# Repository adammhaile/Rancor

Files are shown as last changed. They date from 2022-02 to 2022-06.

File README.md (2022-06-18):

# Rancor 3D Printer

Rancor is a project that came about from being inspired by seeing all the awesome projects at MRRF 2021 and is my first ground-up 3D printer design. It is an IDEX machine with a "spared no expense" and "there's no such thing as too much feature creep" design philosophy. Learning to CNC machine aluminium with my new [MilkCr8 CNC](https://github.com/Makers-On-Tap/milkcr8-cnc) was also a major factor, so if a component *could* be machined out of 1/4" aluminum tooling plate, it was. It was never designed to be manufactured and mainly exists as somethingt to show off.

## Specs

- Cartesian IDEX motion system
- 45 parts custom machined from aluminum tooling plate
- Cold-swappable tools require only 3 bolts and a 14-pin Molex Mini-Fit connector
- 5 currently configured tools that can be used
    - 2x E3D Hemera & Revo
    - 3x E3D Hemera & copper block, Slice 50W heater, Bondtech CHT nozzle (1.0mm, 1.4mm, 1.8mm)
- 330x320x600 mm print volume
- Prusa SuperPINDA ABL probe
- 0.9° LDO 42STH60-2004MAC Motors for each axis
- LDO MGN12 Linear Rails
- PTFE coated LDO leadscrews for Z
- Mandala Rose Works 6.35mm MIC6 cast aluminum bed (Railcore)
- Mandala Rose Works Z axis bed yokes (Railcore)
- Mandala Rose Works Z Oldham Wobblers (Railcore)
- 750W 120V AC Keenovo Bed Heater
- Duet 6HC mainboard with Duet 3HC expansion to drive all 9 motors
- 930x550x960 mm outter dimensions (excluding tool cables)
- 7.9" 400x1280 LCD display for g-code scrolling
- 13.3" 1080x1920 LCD touch display to show the Duet DWC interface
- 2x Raspberry Pi 4 - One for Duet SBC and one running Android for DWC display
- Filament sensors for each tool, based on the Prusa Mini sensor
- Internal network between the two Pi 4's using a Linksys router that provides on-site WiFi
- Ethernet connection for Duet SBC Pi for normal network connectivity
- Teensy 3.2 managed "voice" output controlled via a Duet UART connection

## CAD

All of the CAD for this project was done in Fusion 360 and the files (both F360 and STEP) can be found on [this release page](https://github.com/adammhaile/Rancor/releases/tag/cad_release).

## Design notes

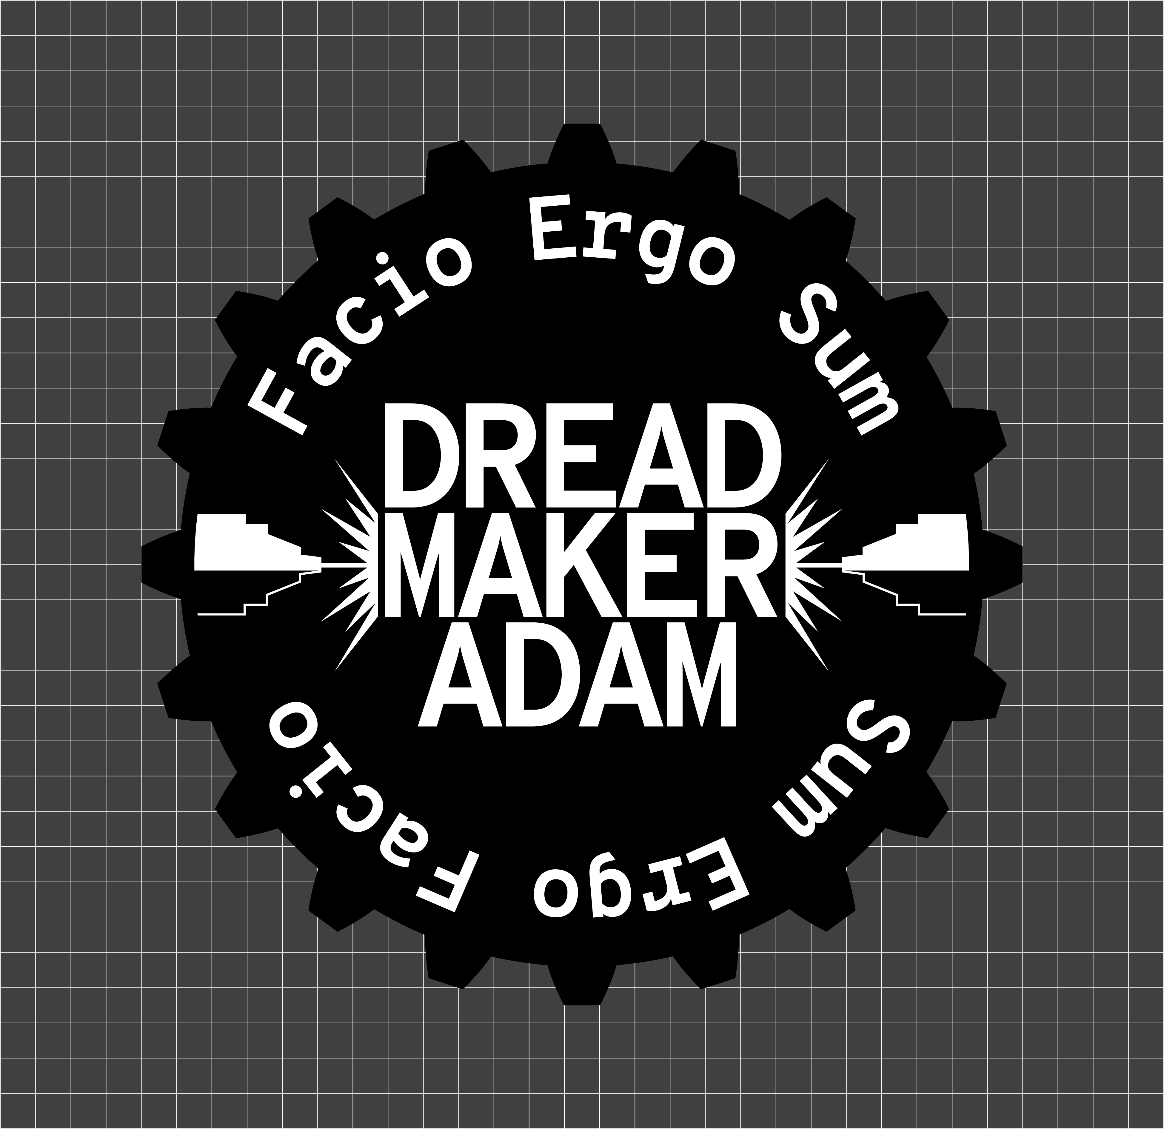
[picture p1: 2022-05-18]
PrusaSlicer/BedTexture.png

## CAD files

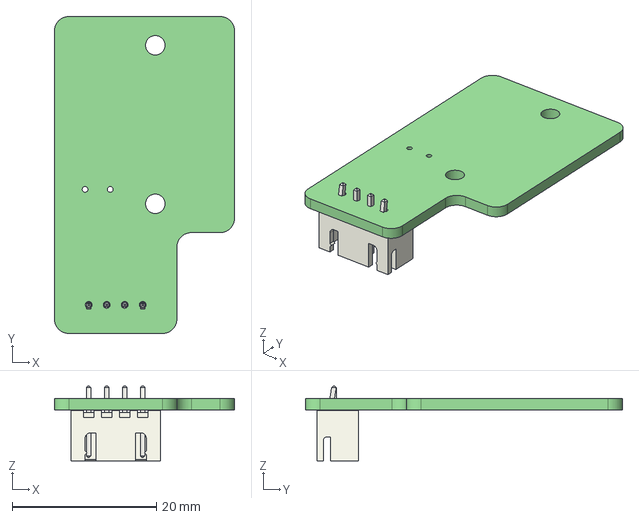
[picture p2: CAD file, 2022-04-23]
larson_vu/larson_vu_pcb/larson_vu_pcb.step
25.0 x 44.0 x 10.4 mm
larson_vu_pcb PCB

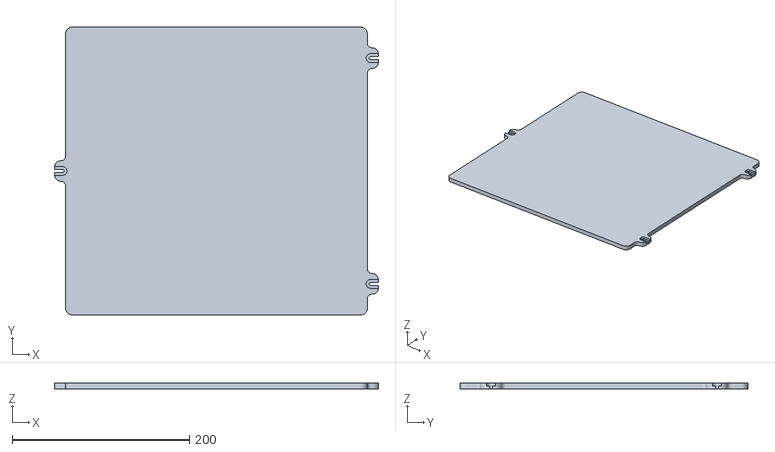
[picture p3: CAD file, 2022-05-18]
PrusaSlicer/BedModel.stl
366.0 x 325.0 x 6.35

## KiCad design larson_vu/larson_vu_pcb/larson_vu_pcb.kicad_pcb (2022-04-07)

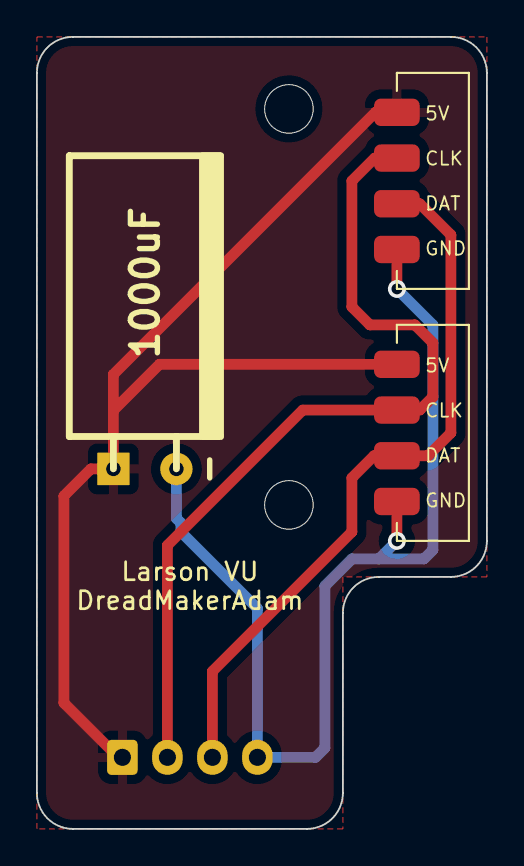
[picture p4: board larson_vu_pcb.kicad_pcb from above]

Board: 2 copper layers, 25.0 x 44.0 mm, 6 parts (1 on the bottom side), 4 nets.

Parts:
C1: 1000uF; CP_8x15mm_horiz-L
H1, H2: MountingHole; MountingHole_2.7mm_M2.5
J1: FromController; JST_XH_B4B-XH-A_1x04_P2.50mm_Vertical
J2, J3: ToStrip; APA102_STRIP

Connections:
5V: C1.1, J1.1, J2.1, J3.1
CLK: J1.2, J2.2, J3.2
DATA: J1.3, J2.3, J3.3
GND: C1.2, J1.4, J2.4, J3.4

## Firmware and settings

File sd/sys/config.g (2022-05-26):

; Load global vars
M98 P"globals.g"

; General preferences
G90                                                         ; send absolute coordinates...
M83                                                         ; ...but relative extruder moves
M550 P"Rancor"                                              ; set printer name

; Larson VU Serial Config
M575 P1 B57600 S2                                           ; Setup UART on IO_0 to 57600 baud

; Audio Player Serial Config
M575 P2 B57600 S2                                           ; Setup UART on IO_1 to 57600 baud

; Setup Lights
M950 P0 C"0.out9" Q4000

; Setup Servos
M950 S1 C"0.io7.out"
M280 P1 S100

; Wait a moment for the CAN expansion boards to start
G4 S2

; Drives
M569 P0.0 S0                                                ; Left Y
M569 P0.1 S1                                                ; Left X
M569 P0.2 S0                                                ; Left Extruder
M569 P0.3 S1                                                ; Left Z
M569 P0.4 S1                                                ; Right Rear Z
M569 P0.5 S1                                                ; Right Front Z
M569 P1.0 S1                                                ; Right Y
M569 P1.1 S1                                                ; Right X
M569 P1.2 S0                                                ; Right Extruder

M584 X0.1 U1.1 Y0.0:1.0 Z0.3:0.4:0.5 E0.2:1.2               ; set drive mapping
M350 X16 U16 Y16 Z16 E16:16 I1                              ; configure microstepping with interpolation
M92  X160 U160 Y160 Z1600 E397:397                          ; set steps per mm
M566 X400 U400 Y400 Z100 E1500:1500                         ; set maximum instantaneous speed changes (mm/min)
M203 X10800 U10800 Y10800 Z900 E3600:3600                   ; set maximum speeds (mm/min)
M201 X500 U500 Y500 Z100 E1500                             	; set accelerations (mm/s^2)
M906 X1400 U1400 Y1400 Z1200 E1100:1100 I75                 ; set motor currents (mA) and motor idle factor in per cent
;M84 S30                                                    ; Set idle timeout

;Leadscrew locations
M671 X-13.7:343.8:343.8 Y160:287.5:32.5 S7.5

; Axis Limits
; TODO - these are wild guesses at this point for X
; will need to change mins to negatives
M208 S1 X-85 U0 Y0 Z-2                                            ; set axis minima
M208 S0 X405 U450 Y345 Z{global.zsize}                            ; set axis maxima

; Endstops
M574 X1 S1 P"0.io2.in"                                        ; X homes low end
M574 U2 S1 P"1.io2.in"                                        ; U homes high end
M574 Y1 S1 P"0.io3.in+1.io3.in"                               ; Y has dual motors and endstops
; TODO - setup homing files https://duet3d.dozuki.com/Wiki/ConfiguringMultipleIndependentXcarriagesCartesian#Section_Homing_files

; Z-Probe
M558 P5 C"^0.io5.in" H2.5 F250 T6000                            ; set Z probe type to switch and the dive height + speeds
G31 P500 X0 Y0 Z1.2                                   ; set Z probe trigger value, offset and trigger height
M557 X15:315 Y20:300 S75:70                                    ; define mesh grid

; Heaters
; Bed
M308 S0 P"0.temp0" Y"thermistor" T100000 B4240                ; configure sensor 0 as thermistor on pin temp0
M950 H0 C"0.out0" T0                                          ; create bed heater output on out0 and map it to sensor 0
M307 H0 B0 R0.611 C647.0 D2.25 S1.00                          ; enable bang-bang mode for the bed heater and set PWM limit
M140 H0                                                     ; map heated bed to heater 0
M143 H0 S120                                                ; set temperature limit for heater 0 to 120C

; Left
M308 S1 P"0.temp1" Y"thermistor" T100000 B4725 C7.06e-8       ; configure sensor 1 as thermistor on pin temp1
M950 H1 C"0.out1" T1                                          ; create nozzle heater output on out1 and map it to sensor 1
; M307 H1 R2.616 K0.237:0.348 D5.69 E1.35 S1.00 B0 V23.9      ; disable bang-bang mode for heater  and set PWM limit
; M143 H1 S285                                                ; set temperature limit for heater 1 to 280C

; Right
M308 S2 P"1.temp0" Y"thermistor" T100000 B4725 C7.06e-8     ; configure sensor 2 as thermistor on pin 1.temp0
M950 H2 C"1.out0" T2                                        ; create nozzle heater output on 1.out0 and map it to sensor 2
; M307 H1 R2.616 K0.237:0.348 D5.69 E1.35 S1.00 B0 V23.9      ; disable bang-bang mode for heater  and set PWM limit
; M143 H2 S285                                                ; set temperature limit for heater 2 to 280C

; Fans
; left HEF
M950 F0 C"0.out7"                                             ; create fan 0 on pin out7 and set its frequency
M106 P0 S1 H1 T45                                         ; set fan 0 value. Thermostatic control is turned on
; Left PCF
M950 F1 C"0.out8"                                             ; create fan 1 on pin out8 and set its frequency
M106 P1 S0 H-1                                              ; set fan 1 value. Thermostatic control is turned off
; Right HEF
M950 F2 C"1.out7"                                           ; create fan 2 on pin 1.out7 and set its frequency
M106 P2 S1 H2 T45                                         ; set fan 2 value. Thermostatic control is turned on
; Right PCF
M950 F3 C"1.out8"                                           ; create fan 3 on pin 1.out8 and set its frequency
M106 P3 S0 H-1                                               ; set fan 3 value. Thermostatic control is turned on

; Tools
; Left
M563 P0 S"Left" D0 X0 H1 F1                                    ; define tool 0
; G10 P0 X-71.5 Y-20.6 Z0                                        ; set tool 0 axis offsets
G10 P0 X0 Y0 Z0
G10 P0 R0 S0                                                   ; set initial tool 0 active and standby temperatures to 0C

M591 D0 P1 C"0.io4.in" S0								; setup T0 filament sensor

; Right
M563 P1 S"Right" D1 X3 H2 F3                                   ; define tool 1
; G10 P1 U-0.3 Y-20.6 Z0.35                                      ; set tool 1 axis offsets
G10 P1 U0 Y0 Z0
G10 P1 R0 S0                                                   ; set initial tool 1 active and standby temperatures to 0C

M591 D1 P1 C"1.io5.in" S0								; setup T1 filament sensor

; extra sensors
M308 S10 Y"mcu-temp" A"MCU"                           ; defines sensor 10 as MCU temperature sensor

; set base tool names
M98 P"tools/t0.g" 
M98 P"tools/t1.g"
M98 P"tools/bed.g"

; load variable tool configs
M98 P"tools/setup.g"

; Ensure T0 loaded
M98 P"soft_load_tool.g" S0

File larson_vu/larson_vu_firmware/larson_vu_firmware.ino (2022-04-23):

#include <FastLED.h>

#include <EEPROM.h>
#include <Arduino.h>

template <class T>
int EEPROM_writeAnything(int ee, const T &value)
{
    const byte *p = (const byte *)(const void *)&value;
    unsigned int i;
    for (i = 0; i < sizeof(value); i++)
        EEPROM.write(ee++, *p++);
    return i;
}

template <class T>
int EEPROM_readAnything(int ee, T &value)
{
    byte *p = (byte *)(void *)&value;
    unsigned int i;
    for (i = 0; i < sizeof(value); i++)
        *p++ = EEPROM.read(ee++);
    return i;
}

#define ANIM_AUDIO 0
#define ANIM_LARSON_RED 1
#define ANIM_LARSON_ORANGE 2
#define ANIM_LARSON_YELLOW 3
#define ANIM_LARSON_GREEN 4
#define ANIM_LARSON_BLUE 5
#define ANIM_LARSON_PURPLE 6
#define ANIM_LARSON_RAINBOW 7

#define MODE_OFF 0
#define MODE_SOUND 1
#define MODE_LARSON 2
#define MODE_BOTH 3

#define CONFIGCHECK 14
struct config_t
{
    uint8_t mode; // 0=off, 1=sound only, 2=larson only, 3=both
    uint8_t cur_anim;
} config;

void writeConfig()
{
    EEPROM_writeAnything(1, config);
}

void readConfig()
{
    EEPROM_readAnything(1, config);
}

void writeDefaultConfig()
{
    config.mode = MODE_BOTH;
    config.cur_anim = ANIM_LARSON_RED;
}

#define STROBE 4
#define RESET 5
#define DC_One A0
#define DC_Two A1

// audio vars
int FreqL[7];
int FreqR[7];

int SumL = 0;
int SumR = 0;

bool mono_audio = true;

// audio clamp values
#define MIN_LEVEL 100
#define MAX_LEVEL 350
#define OUT_MIN 0
#define OUT_MAX 20

// LED stuff
#define NUM_LEDS 40
#define DATA_PIN SPI_DATA
#define CLOCK_PIN SPI_CLOCK
CRGB leds[NUM_LEDS];

uint8_t led_r_start = (NUM_LEDS / 2);
uint8_t led_l_start = led_r_start - 1;

uint8_t last_anim = 1;

unsigned long last_frame = 0;
#define FRAME_TIME 5

unsigned long last_audio = 0;
#define AUDIO_COOLDOWN 1000

int step = 0;

String serial_input;

/********************Setup Loop*************************/
void setup()
{
    // if (EEPROM.read(0) != CONFIGCHECK)
    // {
    //     EEPROM.write(0, CONFIGCHECK);
    //     writeDefaultConfig();
    // }
    readConfig();

    serial_input = "";

    FastLED.addLeds<SK9822, DATA_PIN, CLOCK_PIN, BGR>(leds, NUM_LEDS).setCorrection(TypicalLEDStrip);
    FastLED.setBrightness(192);

    // Set spectrum Shield pin configurations
    pinMode(STROBE, OUTPUT);
    pinMode(RESET, OUTPUT);
    pinMode(DC_One, INPUT);
    pinMode(DC_Two, INPUT);

    // Initialize Spectrum Analyzers
    digitalWrite(STROBE, LOW);
    digitalWrite(RESET, LOW);
    delay(5);

    Serial.begin(57600);
    // while (!Serial) { delay(1); }

    set_anim(config.cur_anim);
}

void FetchAudio()
{
    digitalWrite(RESET, HIGH);
    delayMicroseconds(200);
    digitalWrite(RESET, LOW);
    delayMicroseconds(200);

    static int freq_amp = 0;
    for (freq_amp = 0; freq_amp < 7; freq_amp++)
    {
        digitalWrite(STROBE, HIGH);
        delayMicroseconds(50);
        digitalWrite(STROBE, LOW);
        delayMicroseconds(50);

        FreqL[freq_amp] = analogRead(DC_One);
        FreqR[freq_amp] = analogRead(DC_Two);
    }

    static int i = 0;
    SumL = SumR = 0;
    for (i = 0; i < 7; i++)
    {
        SumL += FreqL[i];
        SumR += FreqR[i];
    }

    SumL /= 7;
    SumR /= 7;

    SumL = map(SumL, MIN_LEVEL, MAX_LEVEL, OUT_MIN, OUT_MAX);
    SumL = constrain(SumL, OUT_MIN, OUT_MAX);
    SumR = map(SumR, MIN_LEVEL, MAX_LEVEL, OUT_MIN, OUT_MAX);
    SumR = constrain(SumR, OUT_MIN, OUT_MAX);

    if (mono_audio)
    {
        SumR = SumL;
    }
}

void set(uint8_t i, CRGB color)
{
    if (i >= 0 && i < NUM_LEDS)
    {
        leds[i] = color;
    }
}

void anim_audio()
{
    static int x = 0;
    static int c = 0;

    FastLED.clear();

    c = 0;
    for (x = led_l_start; x >= 0; x--)
    {
        if (SumL > c)
        {
            leds[x] = CRGB::Orange;
        }
        else
        {
            break;
        }
        c++;
    }

    c = 0;
    for (x = led_r_start; x < NUM_LEDS; x++)
    {
        if (SumR > c)
        {
            leds[x] = CRGB::Orange;
        }
        else
        {
            break;
        }
        c++;
    }

    FastLED.show();
}

uint8_t larson_tail = 15;
int8_t larson_dir = -1;
uint8_t larson_fade = 256 / (larson_tail + 2);
uint8_t larson_divider = 6;
uint8_t larson_sub_step = 0;

void set_anim(uint8_t i)
{
    step = 0;
    config.cur_anim = i;
    last_anim = i;
    larson_dir = -1;
    writeConfig();
}

void anim_larson(CRGB color, bool rainbow = false)
{
    static uint8_t i = 0;
    static int anim_step = 0;
    static uint8_t fade_val = 0;
    static uint8_t hue = 0;

    anim_step = step / larson_divider;

    if (rainbow)
    {
        hue = map(anim_step, 0, NUM_LEDS - 1, 0, 255);
        hue = (hue + larson_sub_step) % 255;
        hsv2rgb_rainbow(CHSV(hue, 255, 255), color);
    }

    set(anim_step, color);

    for (i = 1; i <= larson_tail; i++)
    {
        fade_val = 255 - (larson_fade * i);
        set(anim_step - i, color.nscale8(fade_val));
        set(anim_step + i, color.nscale8(fade_val));
    }

    step += larson_dir;

    if (anim_step >= NUM_LEDS && larson_dir == 1)
    {
        anim_step = (NUM_LEDS - 1) * larson_divider;
        larson_dir = -1;
    }
    else if (anim_step <= 0 && larson_dir == -1)
    {
        step = 0;
        larson_dir = 1;
        larson_sub_step += 5;
    }
}

void do_update_anim()
{
    if (serial_input.length() >= 2)
    {
        if (char(serial_input[1]) >= 49 && char(serial_input[1]) <= 57)
        {
            Serial.print("A");
            Serial.println(serial_input[1]);
            set_anim(char(serial_input[1]) - 48);
            writeConfig();
        }
    }
}

void do_update_mode()
{
    if (serial_input.length() >= 2)
    {
        if (char(serial_input[1]) >= 48 && char(serial_input[1]) <= 51)
        {
            config.mode = char(serial_input[1]) - 48;
            Serial.print("M");
            Serial.println(config.mode);
            writeConfig();
        }
    }
}

void check_serial()
{
    if (Serial.available())
    {
        char c = Serial.read();
        if (c == 10) // newline, end of command
        {
            if (serial_input.length() >= 1)
            {
                switch (serial_input[0])
                {
                case 'A':
                    do_update_anim();
                    break;
                case 'M':
                    do_update_mode();
                    break;
                }
            }
            serial_input = "";
        }
        else
        {
            serial_input += c;
        }
    }
}

void loop()
{
    if(config.mode == MODE_BOTH || config.mode == MODE_SOUND)
    {
        FetchAudio();
    }
    
    check_serial();
    
    if(config.mode == MODE_OFF)
    {
        FastLED.clear();
        FastLED.show();
        delay(5);
        return;
    }

    if (SumL > 0 || SumR > 0)
    {
        last_audio = millis();
    }
    
    if (millis() - last_audio < AUDIO_COOLDOWN && (config.mode == MODE_BOTH || config.mode == MODE_SOUND))
    {
        config.cur_anim = ANIM_AUDIO;
    }
    else if (config.cur_anim == ANIM_AUDIO)
    {
        set_anim(last_anim);
    }

    if (millis() - last_frame > FRAME_TIME)
    {
        last_frame = millis();
        FastLED.clear();
        
        if(config.mode == MODE_BOTH || config.mode == MODE_LARSON)
        {
            switch (config.cur_anim)
            {
            case ANIM_LARSON_RED:
                anim_larson(CRGB::Red);
                break;
            case ANIM_LARSON_ORANGE:
                anim_larson(CRGB::Orange);
                break;
            case ANIM_LARSON_YELLOW:
                anim_larson(CRGB::Yellow);
                break;
            case ANIM_LARSON_GREEN:
                anim_larson(CRGB::Green);
                break;
            case ANIM_LARSON_BLUE:
                anim_larson(CRGB::Blue);
                break;
            case ANIM_LARSON_PURPLE:
                anim_larson(CRGB::Purple);
                break;
            case ANIM_LARSON_RAINBOW:
                anim_larson(CRGB(), true);
                break;
            default:
                anim_audio();
                break;
            }
        }
        else
        {
            anim_audio();
        }
        FastLED.show();
    }
}

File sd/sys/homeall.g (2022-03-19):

; homeall.g

M98 P"soft_load_tool.g" S0 ;ensure T0 selected

set global.cur_tool = {global.t0tool} ;force because tpost0 doesn't run

G91                                 ; relative positioning
G1 H2 Z{global.zclearance} F{global.speed_xy}     ; lift Z relative to current position
G1 H1 X{-global.xu_seek} U{global.xu_seek} Y{-global.y_seek} F{global.speed_xyhome_fast}        ; move quickly to X and Y axis endstops and stop there (first pass)
G1 H2 X5 U-5 Y5 F{global.speed_xy/2}               ; go back a few mm
G1 H1 X{-global.xu_seek} U{global.xu_seek} Y{-global.y_seek} F{global.speed_xyhome_slow}         ; move slowly to X and Y axis endstops once more (second pass)

G1 X1 Y1 U-1 F{global.speed_xy/2}   ; back off from endstops
G90                                 ; absolute positioning

; use G53 below because it needs to be relative to the probe
G53 G1 X{global.xcenter} Y{global.ycenter} F{global.speed_xy} ;position probe above center

M558 F{global.speed_zhome_fast}
G30

M558 F{global.speed_zhome_slow}
G30

G91
G1 Z{global.zclearance} F{global.speed_z}
G90

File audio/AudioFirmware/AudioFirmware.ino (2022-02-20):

#include "VS1053.h"

#define USB Serial
#define Duet Serial1
#define LED 13

String input; 


void setup() {
  USB.begin(115200); //USB Serial
  Duet.begin(57600); // IO Serial - connected to Duet via IO_1
//  while (!USB) { delay(1); }
  delay(500);

  pinMode(LED, OUTPUT);
  digitalWrite(LED, HIGH);

  begin_audio();

  input = "";
}

void do_play(String filename)
{
  USB.println("PLAY: " + filename);
  if(play_audio(filename))
  {
    for(long i=0;i<5;i++)
    {
      digitalWrite(LED, HIGH);
      delay(750);
      digitalWrite(LED, LOW);
      delay(250);
    }
  }
  else
  {
    for(long i=0;i<10;i++)
    {
      digitalWrite(LED, HIGH);
      delay(500);
      digitalWrite(LED, LOW);
      delay(250);
    }
  }
}

void loop() {
  if(NO_SD)
  {
    digitalWrite(LED, HIGH);
    delay(500);
    digitalWrite(LED, LOW);
    delay(500);
  }
  else if(NO_PLAYER)
  {
    digitalWrite(LED, HIGH);
    delay(1000);
    digitalWrite(LED, LOW);
    delay(200);
  }
  else if(Duet.available()) {
    char c = Duet.read();
    if(c == 10) // newline, end of command
    {
      do_play(input);
      input = "";
    }
    else
    {
      input += c;
    }
  }
}

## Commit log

2022-02-20 add sd sync
    [bed.g, config.g, homeall.g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]
2022-02-20 Add audio files/firmware
    [homeall.g]
2022-02-22 Add more sound options
    [M800.g, config.g]
2022-03-03 update sync
    [M800.g]
2022-03-11 Functional motion config
    [bed.g, config.g, heightmap.csv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]
2022-03-11 Add startup level
    [heightmap.csv]
2022-03-13 Make gcode scroller keep running if DSF restarts
    [config.g, heightmap.csv, homeall.g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]
2022-03-13 variable-ize the shit out of everything
    [bed.g, config.g, globals.g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]
2022-03-14 Add random audio handling in arduino
2022-03-16 config backup
    [config.g, heightmap.csv, pause.g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]
2022-03-18 sd backup
    [cancel.g, config.g, full_park.g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]
2022-03-18 wipe/purge routines
    [globals.g, t0wipe.g, t1wipe.g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]
2022-03-19 filament management and dynamic tools
    [config.g, filament.g, filament_load.g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]
2022-03-19 Tweaks to filament handling
    [config.g, filament.g, filament_load.g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]
2022-03-19 Add park macro
    [filaments.csv, heightmap.csv]
2022-03-31 Audio export now mono
    [larson_vu.kicad_pcb, larson_vu.kicad_sch]
2022-03-31 Added larson scanner PCB
    [larson_vu-B_Cu.gbl, larson_vu-B_Mask.gbs, larson_vu-B_Silkscreen.gbo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]
2022-04-01 better tool and filament handling
    [M800.g, M801.g, cancel.g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]
2022-04-04 Add automated tool provisioning
    [config.g, filament.g, filaments.csv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]
2022-04-05 config update
    [config.g, filament.g, filaments.csv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]
2022-04-07 new LED strip board
    [larson_vu-B_Cu.gbl, larson_vu-B_Mask.gbs, larson_vu-B_Silkscreen.gbo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]
2022-04-08 larson_vu switch between larson and audio
2022-04-23 Tweak VU firmware
    [larson_vu_pcb.step]
2022-04-29 Backup from failed SD
    [M800.g, M801.g, bed.g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]
2022-04-29 tweak gcode scroller run
    [config.g]
2022-05-05 Update offsets
    [config.g, filaments.csv, heightmap.csv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]
2022-05-15 Bed and prime config system
    [0.4.g, bed.g, bed_offsets.g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]
2022-05-15 Set prime for all
    [config.g]
2022-05-18 Add slicer config
    [BedModel.stl]
2022-05-22 Adding calibration test files
2022-05-26 ignore csv files
    [bed.g, bed_offsets.g, filaments.csv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]
2022-05-26 Add gcode scroller boot sequence
    [config.g]
2022-06-04 Add direct timelapse control from journal polling
    [0.8.g, M4200.g, M4201.g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]
2022-06-05 sys sync
    [filament.g, present.g]
2022-06-06 Fix timing for final video record
    [present.g, stop.g]
2022-06-18 Add CAD file release info
2022-10-15 Add 0.6 nozzle configs
    [0.6.g, config.g, filament.g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]
